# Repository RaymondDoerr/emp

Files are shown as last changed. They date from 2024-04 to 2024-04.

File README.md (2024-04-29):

# **EMP - The Excessively Magnetic Panel Mod**

Jump to: 
- [BOM and Tool List](#boms-and-tool-lists)
- [Magnet Tolerance Test](#the-magnet-tolerance-test)
- [STL Print Requirements](#stl-print-requirements)
- [Assembly](#assembly)
- [Installation](#installation)

## Description:
This mod converts every panel on the Voron to a well sealed, removable magnetic doors with all-magnetic >180° (Closer to 200°) degree hinges. All panels function as doors and are removable with no hardware what so ever, just yank 'em out!

### Quick Youtube Demo:
Demo Video (https://youtu.be/oXtChmSKKyE)

### Real Life Install Photos
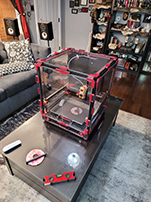
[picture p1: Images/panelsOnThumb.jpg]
Panels On
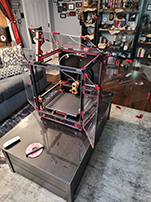
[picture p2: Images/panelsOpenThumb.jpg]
Panels Open
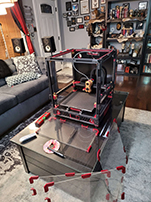
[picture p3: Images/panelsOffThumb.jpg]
Panels Off
  

### Pros:
- You can remove and reinstall all the panels in under a minute.
- Converts all 5 panels into doors with magnetic "no hardware" hinges.
- No-Glue design.
- Magnets are designed to pull into their print rather than out. So no popped out magnets!
- Provides a good chamber seal with a seal thats easy to inspect and look for gaps/flaws.
- Extremely customizable, install the mod on all the panels, only the doors, just the top, whatever you want. Mix and match!
- Pulls the panels 6mm out from the extrusions, meaning less of a chance the cable chains, hot end, wiring and other parts hitting your panels and scratching them.

### Cons:
- VHB tape. (Better than drilling holes I guess?)
- Requires a *ton* of magnets. (Approx. 188 to 236)
- While the hinges work well, they can sometimes sag a bit on the side panels just due to the overall weight. But this is just cosmetic.
- Early days of the install you may get annoyed at panel clips popping off the VHB tape. Although this is the same problem the standard Voron doors have.
- Easy install, but tedious due to so many little parts.
- The Weather seal used is a bit expensive, and not a standard Voron BOM part. (See [BOM and Tool List](#boms-and-tool-lists) for sources)
- Pulling the panels 6mm out from the extrusions has a possibility of interfering with some mods that expect the standard Voron doors and panels.

There are 2 variants of this panel mod:

### "All Doors"
This is the intended original design. Requires more magnets and hardware, but allows you to open every single panel on your Voron (including the back and top!) like a hinged door or just yank them all off with no hardware.

### "Voron Spec"
Exactly the same configuration as standard Voron panels, except with all the benefits of the magnet panels and hinges. This mod was designed with "All Doors" in mind, but for users who don't want this functionality, using the "Voron Spec" configuration will save you a ton of hardware and simplify installation while still allowing you to yank off all the panels in under 30 seconds.

# BOMs and Tool Lists:

## Tools (You have them already):
- **Small Hammer** for tapping magnets gently into place. Doesn't even have to be a hammer, you should not need much force at all. A rubber mallet also works well.
- **1x m3x20 SHCS or similar length screw** to use with the hammer. You just need an m3 SHCS long enough you can hold it with your fingers while you use the hammer.
- **Flat, solid surface** for hammering.
- **2.5mm Hex Key.**
- **Metric Ruler** at least 10cm long. (Calipers, measuring tape, etc, also work fine.)
- **Scissors** for the VHB tape. You'll want nice, sharp and clean ones.
- **A few seasons of The Office** while assembling the hardware prior to installation. (Can supplement with your show of choice.)

## "All Doors" BOM:
- **236x** - *6x3mm Disc Magnets (Grade n52 Recommended)*
  - [Source: West3d](https://west3d.com/products/6mm-x-3mm-round-neomydium-magnets)
- **89x** - *M3x8mm SHCS Screws*
- **69x** - *Hammerheads, Roll In T-Nuts or Springnuts*, <sub><sup>nice.</sup></sub>
- **20x** - *Roll In T-Nuts or Springnuts (This is in addition to above)*
- **Approx. 2 Meters / 6.7 Feet** - *0.4 Inch VHB Tape*
  - [Source: Lifetime Supply off Amazon](https://www.amazon.com/gp/product/B0CLV11RT9/)
- **Approx. 10 Meters / 33 Feet** - *9mm/8mm Weatherseal* (M-D Brand, Part No. 01025 Recommended)
  - [Source: Amazon](https://www.amazon.com/Multipurpose-Seasons-Marine-Window-Weather/dp/B000HE7YQM) - 2 Packages of 17ft.
  - [U.S. Source: Home Depot](https://www.homedepot.com/p/M-D-Building-Products-17-ft-Black-Small-Rubber-Auto-Marine-Weatherseal-for-All-Climates-01025/202066509) - 2 Packages.
  - [U.S. Source: Ace Hardware](https://www.acehardware.com/departments/building-supplies/weather-stripping-and-window-film/weather-stripping/5315445) - 2 Packages.
  - [U.S. Source: Lowes](https://www.lowes.com/pd/M-D-17-ft-x-11-32-in-Black-Rubber-Foam-Window-Weatherstrip/1038915) - 2 Packages.
  
## "Voron Spec" BOM:
- **188x** - *6x3mm Disc Magnets (Grade n52 Recommended)*
  - [Source: West3d](https://west3d.com/products/6mm-x-3mm-round-neomydium-magnets)
- **71x** - *M3x8mm SHCS Screws*
- **63x** - *Hammerheads, Roll In T-Nuts or Springnuts*
- **8x** - *Roll In T-Nuts or Springnuts (This is in addition to above)*
- **Approx. 1.8 Meters / 5.9 Feet** - *0.4 Inch VHB Tape*
  - [Source: Lifetime Supply off Amazon](https://www.amazon.com/gp/product/B0CLV11RT9/)
- **Approx. 10 Meters / 33 Feet** - *9mm/8mm Weatherseal* (M-D Brand, Part No. 01025 Recommended)
  - [Source: Amazon](https://www.amazon.com/Multipurpose-Seasons-Marine-Window-Weather/dp/B000HE7YQM) - 2 Packages of 17ft.
  - [U.S. Source: Home Depot](https://www.homedepot.com/p/M-D-Building-Products-17-ft-Black-Small-Rubber-Auto-Marine-Weatherseal-for-All-Climates-01025/202066509) - 2 Packages.
  - [U.S. Source: Ace Hardware](https://www.acehardware.com/departments/building-supplies/weather-stripping-and-window-film/weather-stripping/5315445) - 2 Packages.
  - [U.S. Source: Lowes](https://www.lowes.com/pd/M-D-17-ft-x-11-32-in-Black-Rubber-Foam-Window-Weatherstrip/1038915) - 2 Packages.
  
## Per Panel BOM (Ref. Full Part Descriptions Above):
- *Front Door* (Left and Right, **As Door**)
  - **32 Magnets, 12 Screws, 8 Hammerhead, 4 T-nuts/Springnuts**
- *Side and Top Panels* (**As Door**)
  - **44 Magnets, 17 Screws, 13 Hammerheads, 4 T-nuts/Springnuts**
- *Side and Top Panels* (**As Panel**)
  - **32 Magnets, 12 Screws, 12 Hammerheads**
- *Back Panel* (**As Door**)
  - **40 Magnets, 16 Screws, 12 Hammerheads, 4 T-nuts/Springnuts**
- *Back Panel* (**As Panel**)
  - **28 Magnets, 12 Screws, 12 Hammerheads**
  
## Per STL BOM (Ref. Full Part Descriptions Above):
- *[a]hinge_frame_SIZE.stl*
  - **4 Magnets, 3 Screws, 1 Hammerhead, 2 T-nuts/Springnuts**
- *[a]hinge_frame_bottom_SIZE.stl*
  - **4 Magnets, 2 Screws, 2 Hammerheads**
- *[a]corner_frame_SIZE.stl*
  - **2 Magnets, 2 Screws, 2 Hammerheads**
- *[a]side_frame_SIZE.stl*
  - **2 Magnets, 1 Screw, 1 Hammerhead**
- *hinge_panel_SIZE.stl*
  - **4 Magnets, 40mm VHB tape**
- *door_clip_1_SIZE.stl*
  - **2 Magnets, 20mm VHB tape**
- *door_clip_2_SIZE.stl*
  - **2 Magnets, 20mm VHB tape**
- *corner_panel_SIZE.stl*
  - **2 Magnets, 60mm VHB tape**
- *side_panel_SIZE.stl*
  - **2 Magnets, 20mm VHB tape**
  
# The Magnet Tolerance Test:
## (Don't skip!!)

Print one magnet_test.stl for every filament you plan to use for this mod, some filaments behave surprisingly differently!

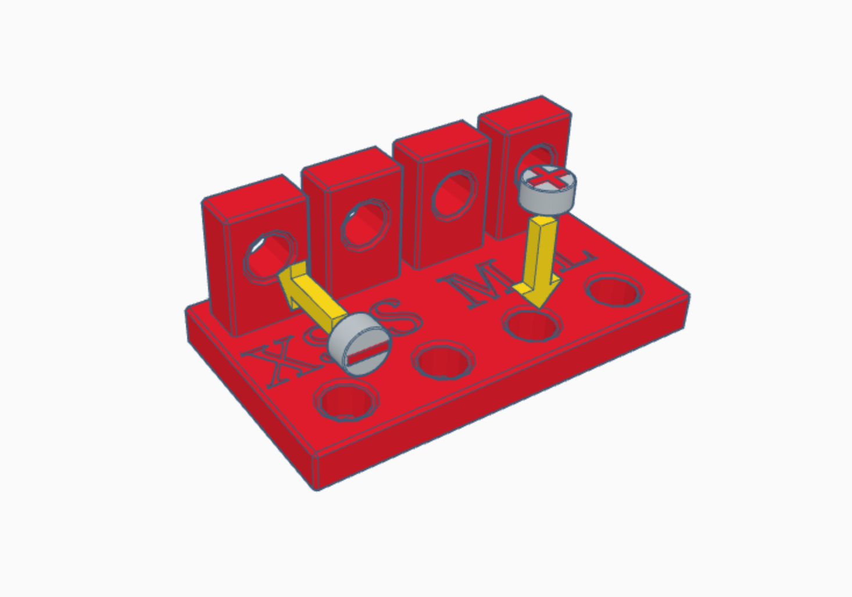
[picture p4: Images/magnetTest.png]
Magnet Test


You are looking for a "snug" but not "tight" fit. You should be able to start the magnets with your hands and some pressure. You **do not** need to seat them all the way down at this step. The fastest way to find the correct holes is to start by inserting a magnet into the *largest* bottom hole (L), if the magnet falls in or can be yanked back out with another magnet, try the next smallest hole. The goal is to find one you can shove part of the way in with your hands and can't be yanked back out with another magnet.

Repeat the same steps on the top/vertical holes. An ideal situation is you pick both the same size holes for the top and bottom. But due to print orientation and everyone's printer being just a little different, you may find yourself needing to go up or down a size on the vertical holes.

The sizes of the holes are as follows:
- XS
  - Horizontal: 6.0mm
  - Vertical: 5.9mm
- S
  - Horizontal: 6.1mm
  - Vertical: 6.0mm
- M (This is what I use)
  - Horizontal: 6.2mm
  - Vertical: 6.1mm
- L 
  - Horizontal: 6.3mm
  - Vertical: 6.2mm

# STL Print Requirements:
After selecting the hole size, now it's time to print the STLs! Select the set of parts that match the hole size you've selected. The top/vertical holes are for the hinges, the horizontal holes were for all other parts.

All prints are designed to print to Voron Spec profiles. If you have warping issues, these parts need very little cooling, all of mine were printed with only about a 5% fan speed on a Stealthburner/G2E/Revo setup. I also ran some experiments and found all the parts can be printed with no cooling what so ever, but YMMV.

All panel STLs have an optional *with_clip* variant you can print, that will add a small lip on the edge of the model making it a bit easier to catch and open the door with your fingers. If you decide to use these, you only need them on the corners you're expecting to open the door from.

## For "All Doors":
### Print with top/vertical hole size:
- **10x** *[a]hinge_frame_SIZE.stl*
- **2x** *[a]hinge_frame_bottom_SIZE.stl*
- **12x** *hinge_panel_SIZE.stl*

### Print with bottom/horizontal hole size:
- **20x** *[a]corner_frame_SIZE.stl*
- **15x** *[a]side_frame_SIZE.stl*
- **2x** *door_clip_1_SIZE.stl*
- **2x** *door_clip_2_SIZE.stl*
- **20x** *corner_panel_SIZE.stl*
- **11x** *side_panel_SIZE.stl*

## For "Voron Spec":
### Print with top/vertical hole size:
- **4x** *[a]hinge_frame_SIZE.stl*
- **4x** *hinge_panel_SIZE.stl*

### Print with bottom/horizontal hole size:
- **20x** *[a]corner_frame_SIZE.stl*
- **19x** *[a]side_frame_SIZE.stl*
- **2x** *door_clip_1_SIZE.stl*
- **2x** *door_clip_2_SIZE.stl*
- **20x** *corner_panel_SIZE.stl*
- **15x** *side_panel_SIZE.stl*

# Assembly:
## Magnets
First step is to insert all of the magnets into all of the STLs. It's very important to get the polarity correct. Be aware of the orientation of the parts in the example images.

I've found the best method to insert the magnets is to hand push in the magnet until it's halfway in, and then use the head of an M3x14mm screw and attach it to the magnet, then lightly tap the magnet down in place with a hammer. It makes assembly go much faster. Just be sure to use a flat surface so you don't blow the magnet straight through the hole!

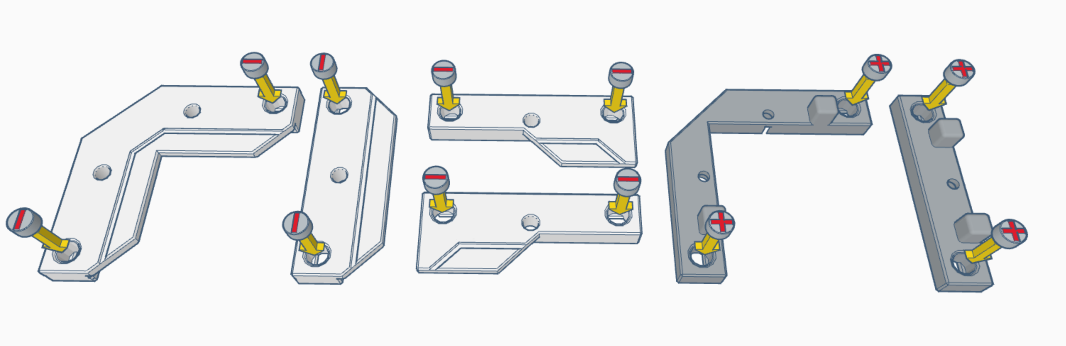
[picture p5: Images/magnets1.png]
Magnet Test

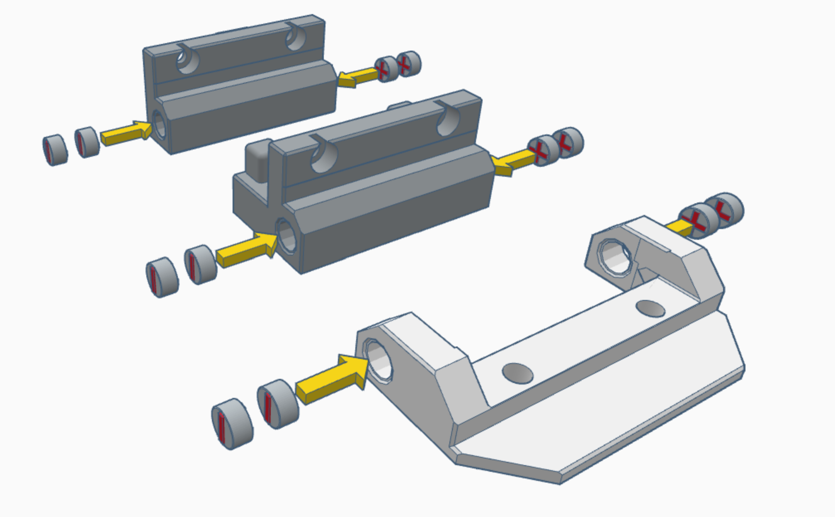
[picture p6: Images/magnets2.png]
Magnet Test


## Hardware
You may preload all the hardware **EXCEPT FOR** the T-nuts noted in red. These must be loaded into the extrusions and slid into place **after** installation of the door hinge.

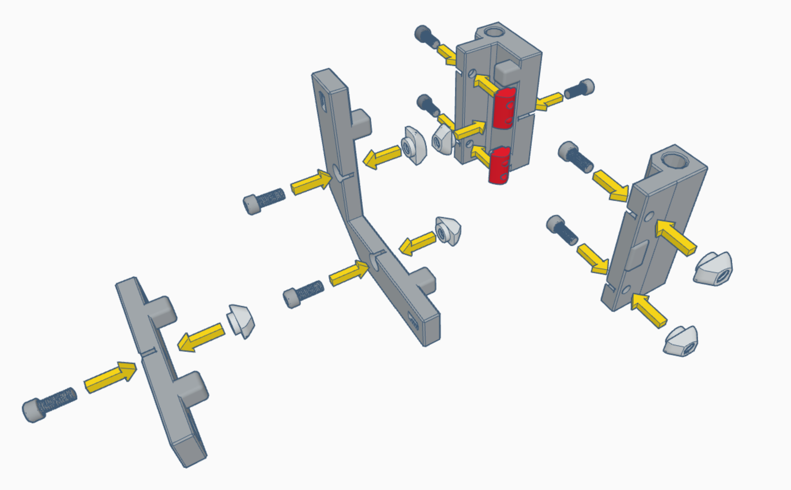
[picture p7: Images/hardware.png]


## VHB Tape
Don't skimp on the VHB tape! When installed, press down hard on the tape to get a better bond to the clips.

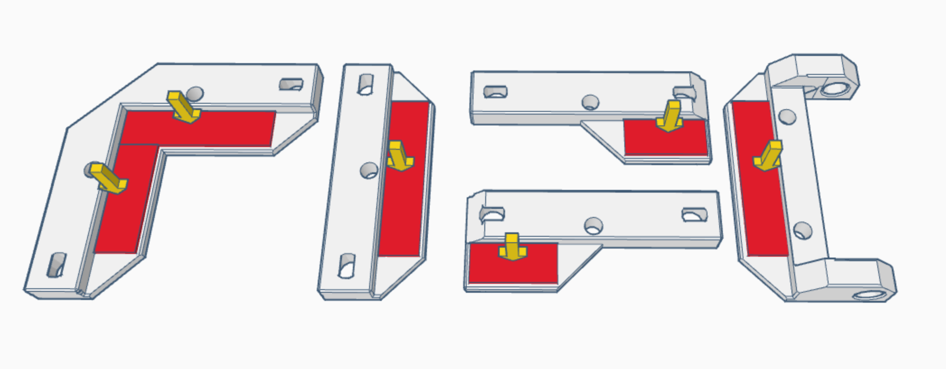
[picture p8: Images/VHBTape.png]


# Installation:

## **INSTALL GUIDE ASSUMES "ALL-DOORS" CONFIGURATION. **
### If you're doing the "Voron Spec" configuration the install guide still applies, **but** you need to supplement the 2x hinges on each panel with 1x side clips, effectively making all 4 sides of the panel symmetrical. All other steps are identical.

### Provided is a direct link to the STL Placement Reference both on Tinkercad and GitHub. Both will show you the location of every STL in 3d space. *Note its not remotely to scale, that's why everything looks ridiculously cramped.*

## View the Full Model STL Placement Reference on:
### [Fully Editable and Color Coded, Tinkercad](https://www.tinkercad.com/things/gM3WwlMIWih-emp-stl-placement-reference)
### [Uneditable and Grey Scale, GitHub](Images/placementReference.stl)

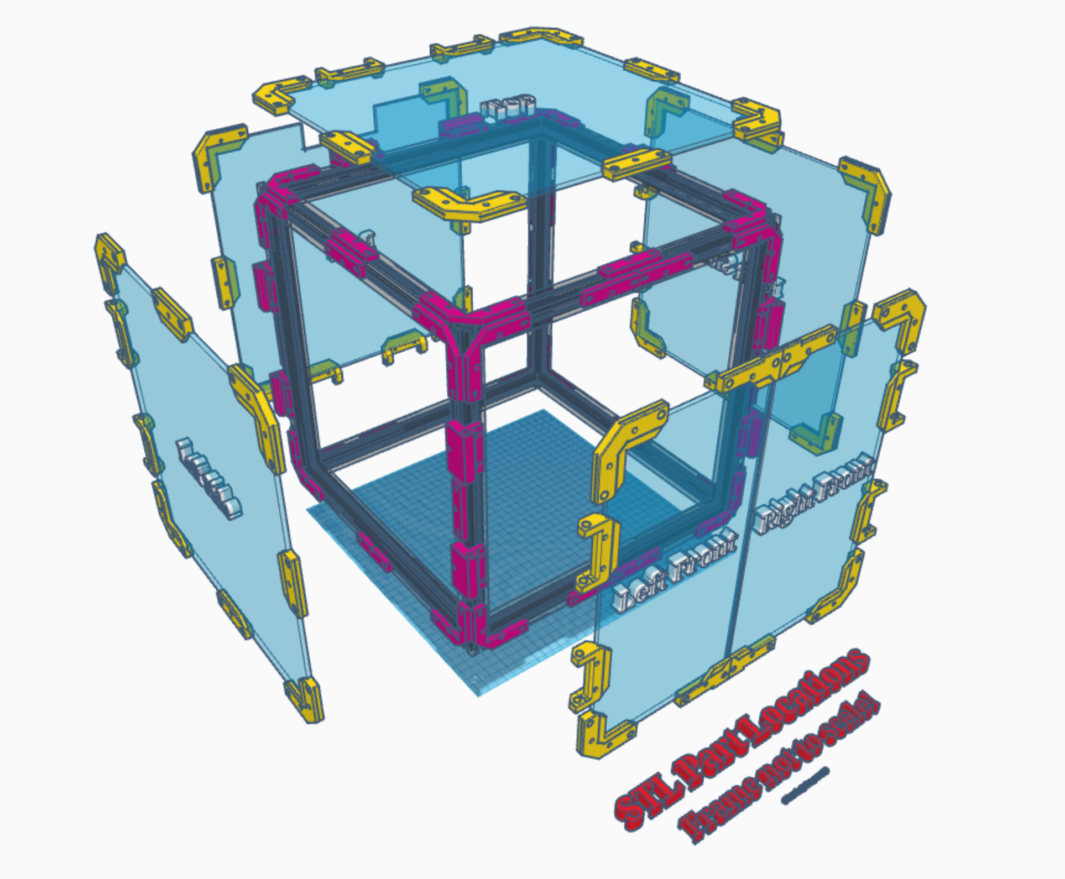
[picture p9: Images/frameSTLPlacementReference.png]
Tinkercad Reference


Refer to the following images or the Tinkercad link above for clip placement on the various panels. Apply significant pressure to the tape to ensure it sticks. In my experience, the VHB tape may be a bit weak the first few days but should all hold together just fine. I like to occasionally revisit this and push the clips down a bit more as I work through the project just to make sure they're staying down.

From here on out, all stl names will be shortened for brevity.

When installing the frame STLs, install them loose initially (just tight enough they don't fall out), you'll use the panels themselves to align the frame STLs in a future step. Place them in the same locations as the panel clips, just on the frame.

**All** Hinges are placed approximately 10cm from the edge of their respective panels.

10cm Hinge Spacing

### Left and Right Side Panels:
- *corner_panel* are placed in the 4 corners of the panel.
- *side_panel* are placed on the top, bottom and front sides of the panel, in the center.
- *hinge_panel* are placed 10cm from the edge of the panel on the back side. 
- Loosely install corner_frame, side_frame and hinge_frame STL files in the same locations as above, but on the extrusions the panel will attach to.

Side Panels Inner
Side Panels Outer

### Top Panel:
- corner_panel.stl are placed in the 4 corners of the panel.
- side_panel.stl are placed on the top, bottom and front sides in the center.
- hinge_panel.stl are placed 10cm from the edge of the panel on the back side. 
- Loosely install corner_frame, side_frame and hinge_frame STL files in the same locations as above, but on the extrusions the panel will attach to.

Top Panel Inner
Top Panel Outer

### Back Panel:
- corner_panel.stl are placed in the 4 corners.
- side_panel.stl are placed on left and right sides in the center.
- hinge_panel.stl are placed 10cm from the edge of the panel on the bottom side. 
- Loosely install corner_frame, side_frame and **hinge_frame_bottom** STL files in the same locations as above, but on the extrusions the panel will attach to.

Back Panel Inner
Back Panel Outer

### Front Doors (Left):
- corner_panel.stl are placed in the left 2 corners.
- hinge_panel.stl are placed 10cm from the edge of the panel on the left side. 
- door_clip_1.stl is placed on the bottom right corner.
- door_clip_2.stl is placed on the top right corner.
- Loosely install corner_frame, side_frame (for door_clip_1 and 2) and hinge_frame STL files in the same locations as above, but on the extrusions the doors will attach to.

### Front Doors (Right):
- corner_panel.stl are placed in the right 2 corners.
- hinge_panel.stl are placed 10cm from the edge of the panel on the right side. 
- door_clip_1.stl is placed on the top left corner.
- door_clip_2.stl is placed on the bottom left corner.
- Loosely install corner_frame, side_frame (for door_clip_1 and 2) and hinge_frame STL files in the same locations as above, but on the extrusions the doors will attach to.

Front Doors Inner
Front Doors Outer

## Attaching to extrusions

- Place one panel at a time on the extrusions and attach them to the loosened frame clips.
- Doublecheck all _frame STLs are magnetically connected to all of the _panel STLs.
- **With the panel installed and attached to the magnets**, tighten the _frame.stl parts **through** the _panel.stls with the guide holes provided. Use your hands to hold the _frame.stl and _panel.stl flush with eachother while tightening for better alignment.

Guide Holes 1
Guide Holes 2

- Anywhere there is a hinge, you may now install the Slide in T-nut or Spring nuts and slide them under the STL and tighten down the screws.

Slide In T-Nuts 1
Slide In T-Nuts 2
Slide In T-Nuts 3
Slide In T-Nuts 4

- Repeat until all panels are fulled installed.

## Installing The Weather Seal
The weather seal is placed on last so you don't accidentally tear it while installing the frame STLs, you want the weather seal placed flush along the inner side of the extrusion. If you purchased the same brand I did, many times the adhesive isn't aligned, use this to your advantage so you don't have any exposed adhesive on the frame.

You **can** place the weather seal on the panel side instead, but you may have issues with the seal pinching against some of the magnetic clips occasionally. Try to put the foam 1-2mm back from the outer edge of the panel to help prevent this.

Seal Placement 1
Seal Placement 2

Installation should be complete at this point. This is where you'll need to look at the overall fit and finish, verify everything looks nice, lined up and even when the doors/panels are installed/closed. 

Be gentle with the hinges for a few days while the VHB tape settles (ie; don't leave them hanging open on their own weight overnight). I like to give the clips a good squish against the panel here and there as I'm working with the printer, just to be sure.

### If you have serious issues with the VHB tape holding to the printed parts post install, there's a few things you can try:
- Try sanding or scratching up the surface of the clip, it will help the VHB tape grab.
- Use something heavy (books, etc) and press the panels into the clips overnight.
- If all else fails and you're working with a filament that just won't stick to the tape no matter what you do, a **very** thin layer of super glue between the tape and panel clips will perma-bond it forever. **Just be extremely careful not to get it on your panels, it'll ruin them!!!** If you must do this, I recommend applying the glue to the clip/tape and letting it fully dry before reattaching them to the panels to avoid any superglue leaking on to the panel. Ideally, no one should have to use glue for anything in this mod. But with 10,000,000 brands of ABS and ASA out there, some may just be more stubborn than others.

# Notes and Supplemental Data
### Tips
- All STL files, except the hinges, can have an additional magnet added if you want to go overkill with magnet strength or have tons of weaker magnets. Note that this will add an enormous amount of extra magnets (Roughly +70-80% more) to the BOM, and if you use n52s it'll be *ridiculously* strong.
- You can rearrange everything, adding or moving hinges and clips where you desire. 
- If you're having issues with the front doors closing (ie; hitting eachother) check to make sure clip_1 and _2 are not overlapping the edge of the panel. Also sometimes just fiddling with the hinges can improve fit and finish.
- If you're using hammerheads for the first time, make sure they actually are holding your part in. They can easily miss the extrusions and just tighten into the plastic.
- The corner_panel/frame STLs on the front doors are technically optional. They're more for ascetics than functionality.
- You can remove 1 magnet from each door_clip_1 and door_clip_2 if you find the front door too strong to open. (Or just use weaker magnets if you have them.)
- You can also remove almost all the side_panel/frame STLs from the entire build, although you may want to double-up on magnets in the corner_panel STLs if it makes the panel too weak. 

### Mod Compatibility
- [The raw STL files on Tinkercad.](https://www.tinkercad.com/things/bFb7dxLxUFV-excessively-magnetic-panel-mod-parts)
- This has not been tested with the [Clicky-Clack Fridge Door Mod](https://github.com/tanaes/whopping_Voron_mods/tree/main/clickyclacky_door), but should theoretically work if you omit the side clips interfering with the Fridge Mod's hinge. There is a possibility it may rub against the side panel. Please let me know if this is an issue!
- This should work with just about any mod that doesn't have an issue with the panels being pushed outwards about 6-8mm from the frame.

### Coming Soon (Before full release)
- A magnetic door handle of some sort.
- Small magnetic arms to prop doors open.

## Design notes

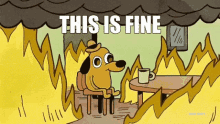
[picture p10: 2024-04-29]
Images/this-is.gif

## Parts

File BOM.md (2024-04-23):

# BOMs and Tool Lists:

## Tools (You have them already):
- **Small Hammer** for tapping magnets gently into place. Doesn't even have to be a hammer, you should not need much force at all. A rubber mallet also works well.
- **1x m3x20 SHCS or similar length screw** to use with the hammer. You just need an m3 SHCS long enough you can hold it with your fingers while you use the hammer.
- **Flat, solid surface** for hammering.
- **2.5mm Hex Key.**
- **Metric Ruler** at least 10cm long. (Calipers, measuring tape, etc, also work fine.)
- **Scissors** for the VHB tape. You'll want nice, sharp and clean ones.
- **A few seasons of The Office** while assembling the hardware prior to installation. (Can supplement with your show of choice.)

## "All Doors" BOM:
- **236x** - *6x3mm Disc Magnets (Grade n52 Recommended)*
  - [Source: West3d](https://west3d.com/products/6mm-x-3mm-round-neomydium-magnets)
- **89x** - *M3x8mm SHCS Screws*
- **69x** - *Hammerheads, Roll In T-Nuts or Springnuts*, <sub><sup>nice.</sup></sub>
- **20x** - *Roll In T-Nuts or Springnuts (This is in addition to above)*
- **Approx. 2 Meters / 6.7 Feet** - *0.4 Inch VHB Tape*
  - [Source: Lifetime Supply off Amazon](https://www.amazon.com/gp/product/B0CLV11RT9/)
- **Approx. 10 Meters / 33 Feet** - *9mm/8mm Weatherseal* (M-D Brand, Part No. 01025 Recommended)
  - [Source: Amazon](https://www.amazon.com/Multipurpose-Seasons-Marine-Window-Weather/dp/B000HE7YQM) - 2 Packages of 17ft.
  - [U.S. Source: Home Depot](https://www.homedepot.com/p/M-D-Building-Products-17-ft-Black-Small-Rubber-Auto-Marine-Weatherseal-for-All-Climates-01025/202066509) - 2 Packages.
  - [U.S. Source: Ace Hardware](https://www.acehardware.com/departments/building-supplies/weather-stripping-and-window-film/weather-stripping/5315445) - 2 Packages.
  - [U.S. Source: Lowes](https://www.lowes.com/pd/M-D-17-ft-x-11-32-in-Black-Rubber-Foam-Window-Weatherstrip/1038915) - 2 Packages.
  
## "Voron Spec" BOM:
- **188x** - *6x3mm Disc Magnets (Grade n52 Recommended)*
  - [Source: West3d](https://west3d.com/products/6mm-x-3mm-round-neomydium-magnets)
- **71x** - *M3x8mm SHCS Screws*
- **63x** - *Hammerheads, Roll In T-Nuts or Springnuts*
- **8x** - *Roll In T-Nuts or Springnuts (This is in addition to above)*
- **Approx. 1.8 Meters / 5.9 Feet** - *0.4 Inch VHB Tape*
  - [Source: Lifetime Supply off Amazon](https://www.amazon.com/gp/product/B0CLV11RT9/)
- **Approx. 10 Meters / 33 Feet** - *9mm/8mm Weatherseal* (M-D Brand, Part No. 01025 Recommended)
  - [Source: Amazon](https://www.amazon.com/Multipurpose-Seasons-Marine-Window-Weather/dp/B000HE7YQM) - 2 Packages of 17ft.
  - [U.S. Source: Home Depot](https://www.homedepot.com/p/M-D-Building-Products-17-ft-Black-Small-Rubber-Auto-Marine-Weatherseal-for-All-Climates-01025/202066509) - 2 Packages.
  - [U.S. Source: Ace Hardware](https://www.acehardware.com/departments/building-supplies/weather-stripping-and-window-film/weather-stripping/5315445) - 2 Packages.
  - [U.S. Source: Lowes](https://www.lowes.com/pd/M-D-17-ft-x-11-32-in-Black-Rubber-Foam-Window-Weatherstrip/1038915) - 2 Packages.

## Per STL BOM (Ref. Full Part Descriptions Above):
- *[a]hinge_frame_<SIZE>.stl*
  - **4 Magnets, 3 Screws, 1 Hammerhead, 2 T-nuts/Springnuts**
- *[a]hinge_frame_bottom_<SIZE>.stl*
  - **4 Magnets, 2 Screws, 2 Hammerheads**
- *[a]corner_frame_<SIZE>.stl*
  - **2 Magnets, 2 Screws, 2 Hammerheads**
- *[a]side_frame_<SIZE>.stl*
  - **2 Magnets, 1 Screw, 1 Hammerhead**
- *hinge_panel_<SIZE>.stl*
  - **4 Magnets, 40mm VHB tape**
- *door_clip_1_<SIZE>.stl*
  - **2 Magnets, 20mm VHB tape**
- *door_clip_2_<SIZE>.stl*
  - **2 Magnets, 20mm VHB tape**
- *corner_panel_<SIZE>.stl*
  - **2 Magnets, 60mm VHB tape**
- *side_panel_<SIZE>.stl*
  - **2 Magnets, 20mm VHB tape**
  
# Ignore below this line, I'm just too lazy to put notes anywhere else at the moment..

### Per STL breakdown for All Doors:
- [a]hinge_frame_<SIZE>.stl
  - 48 Magnets, 36 Screws, 12 Hammerhead, 24 T-nuts
- [a]corner_clip_frame_<SIZE>.stl
  - 40 Magnets, 40 Screws, 40 Hammerheads
- [a]side_clip_frame_<SIZE>.stl
  - 30 Magnets, 15 Screw, 15 Hammerhead
- hinge_panel_<SIZE>.stl
  - 48 Magnets, 480mm VHB tape
- door_clip_1_<SIZE>.stl
  - 4 Magnets, 40mm VHB tape
- door_clip_2_<SIZE>.stl
  - 4 Magnets, 40mm VHB tape
- corner_clip_panel_<SIZE>.stl
  - 40 Magnets, 1200mm VHB tape
- side_clip_panel_<SIZE>.stl
  - 22 Magnets, 220mm VHB tape
  
### Per STL breakdown for Voron Spec:
- [a]hinge_frame_<SIZE>.stl
  - 16 Magnets, 12 Screws, 4 Hammerhead, 8 T-nuts
- [a]corner_clip_frame_<SIZE>.stl
  - 40 Magnets, 40 Screws, 40 Hammerheads
- [a]side_clip_frame_<SIZE>.stl
  - 38 Magnets, 19 Screw, 19 Hammerhead 
- hinge_panel_<SIZE>.stl
  - 16 Magnets, 160mm VHB tape
- door_clip_1_<SIZE>.stl
  - 4 Magnets, 40mm VHB tape
- door_clip_2_<SIZE>.stl
  - 4 Magnets, 40mm VHB tape
- corner_clip_panel_<SIZE>.stl
  - 40 Magnets, 1200mm VHB tape
- side_clip_panel_<SIZE>.stl
  - 30 Magnets, 300mm VHB tape

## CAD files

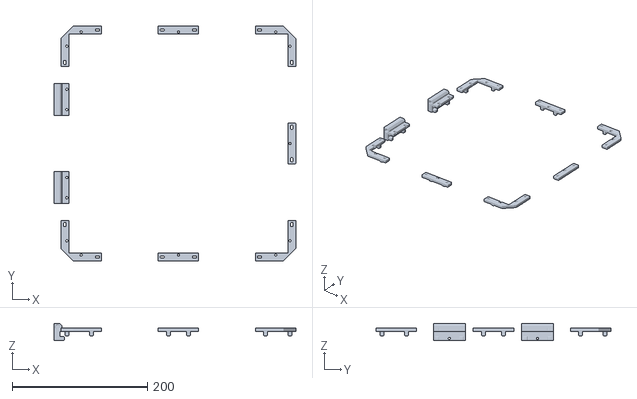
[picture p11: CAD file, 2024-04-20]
Images/placement_reference.stl
358.2 x 348.0 x 25.2

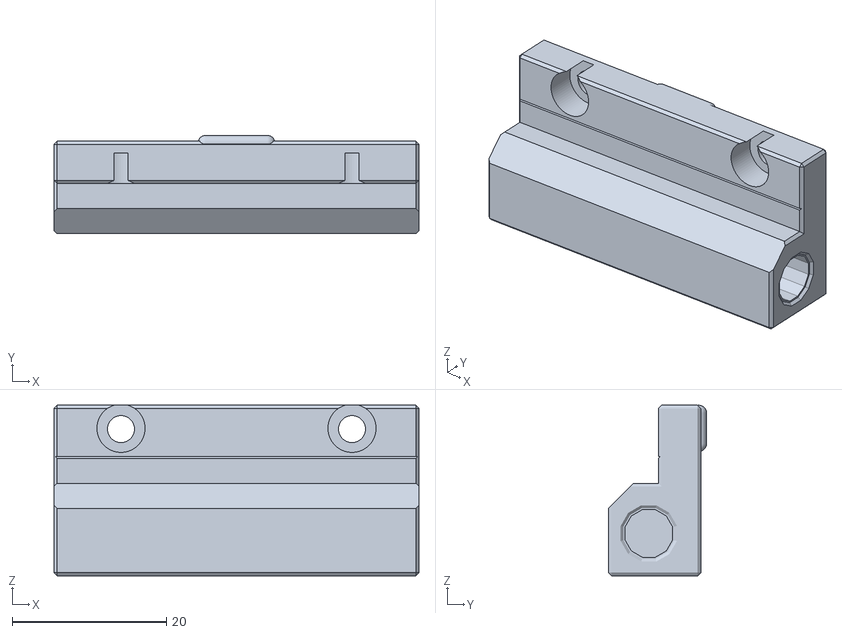
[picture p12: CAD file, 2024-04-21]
STL/alphaSTLs/[a]hinge_frame_bottom_l.stl
47.4 x 12.8 x 22.1

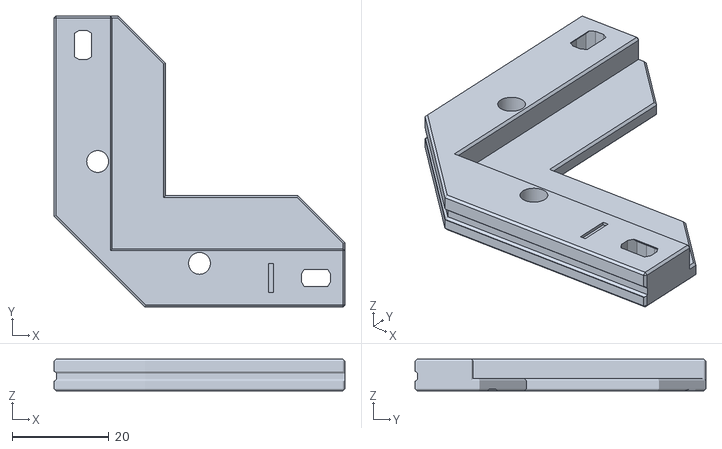
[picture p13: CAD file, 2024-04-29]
STL/extra_small/corner_panel_extra_small.stl
60.0 x 60.0 x 6.50

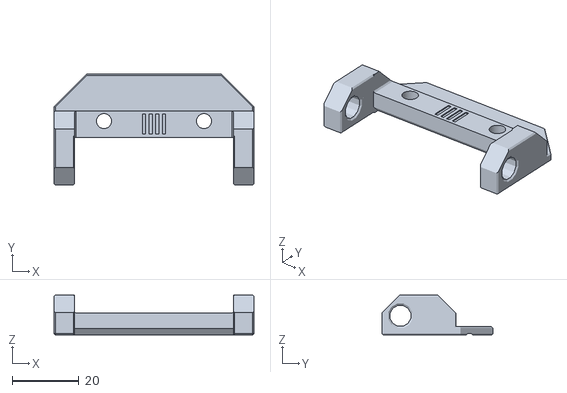
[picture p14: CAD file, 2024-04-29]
STL/large/hinge_panel_large.stl
60.0 x 33.2 x 12.0

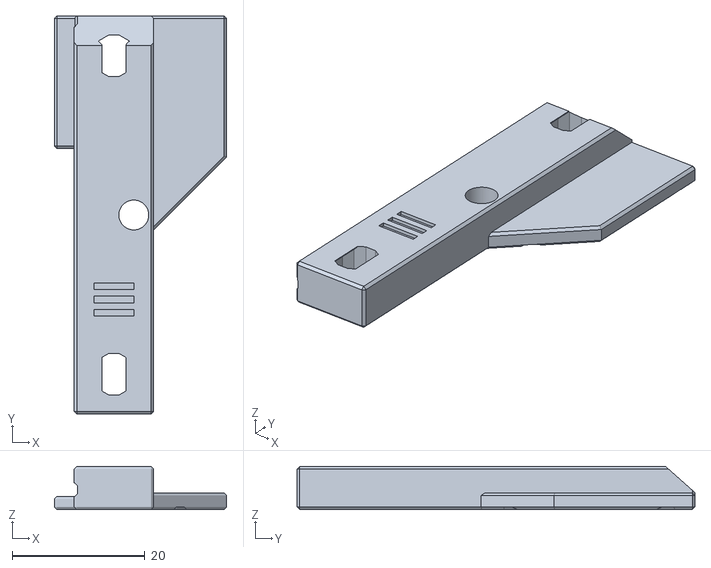
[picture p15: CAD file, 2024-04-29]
STL/medium/door_clip_2_medium.stl
26.0 x 60.0 x 6.50

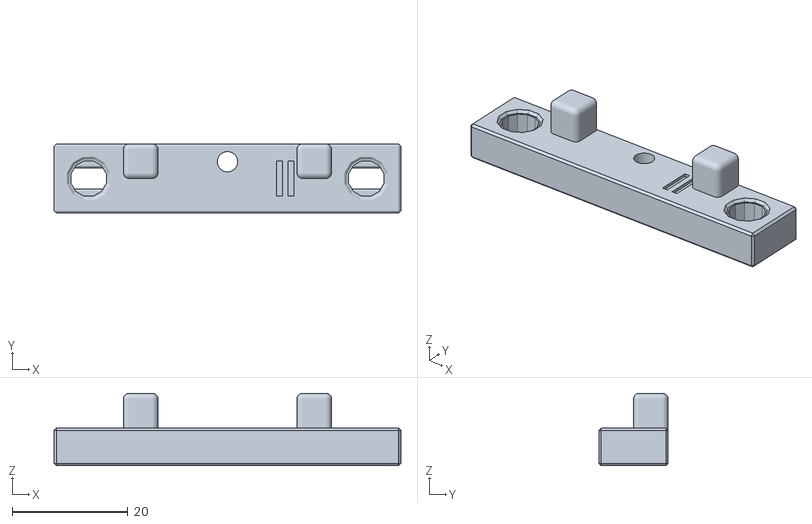
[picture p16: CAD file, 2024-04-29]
STL/small/[a]side_frame_small.stl
60.0 x 12.0 x 12.5

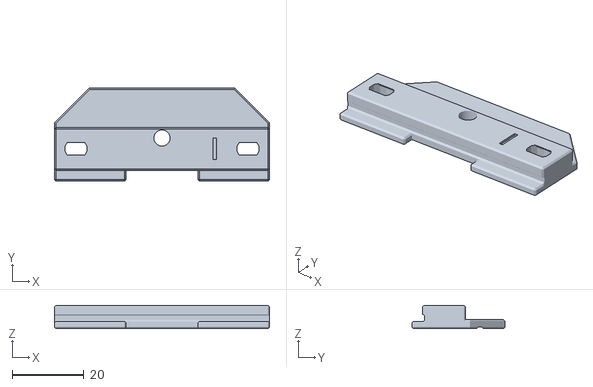
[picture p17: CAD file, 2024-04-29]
STL/extra_small/side_panel_with_clip_extra_small.stl
60.0 x 26.0 x 6.50

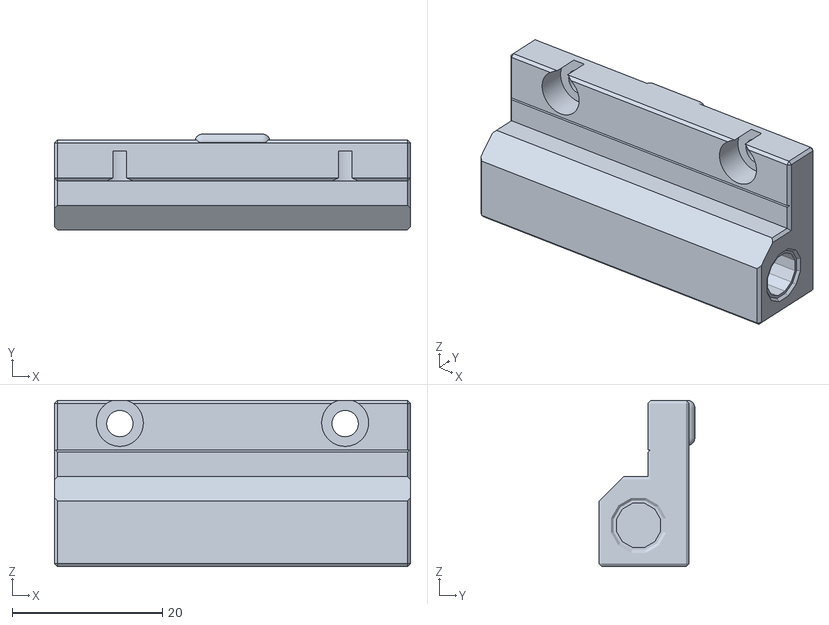
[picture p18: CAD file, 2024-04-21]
STL/alphaSTLs/[a]hinge_frame_bottom_xs.stl
47.4 x 12.8 x 22.1

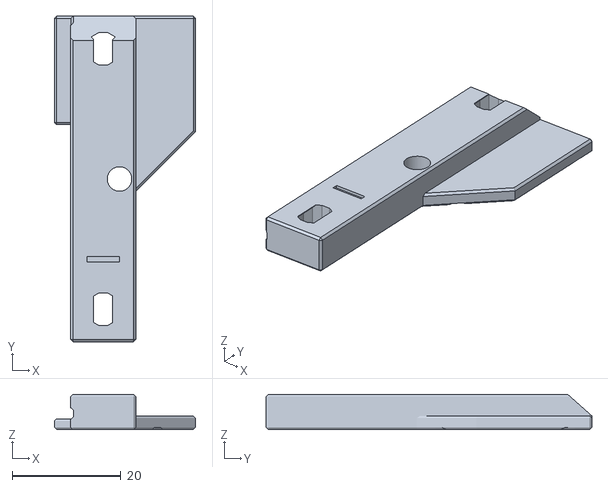
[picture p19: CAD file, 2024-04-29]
STL/extra_small/door_clip_2_extra_small.stl
26.0 x 60.0 x 6.50

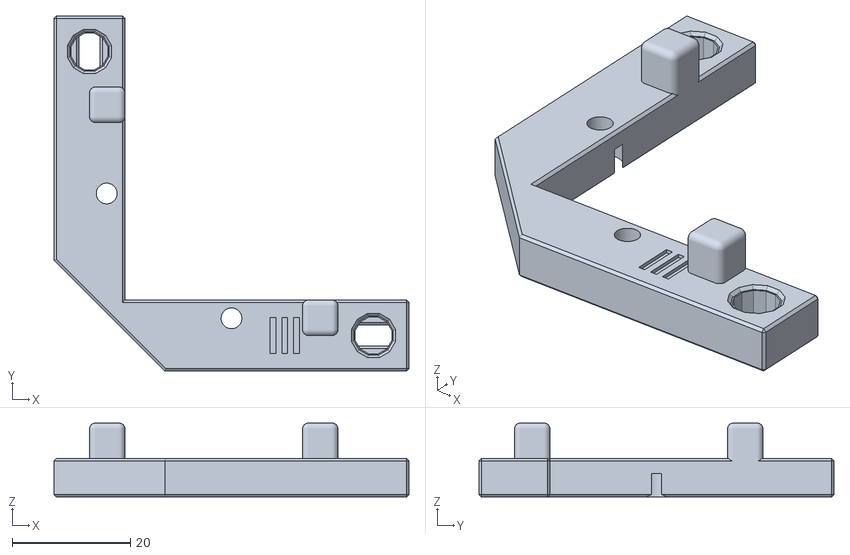
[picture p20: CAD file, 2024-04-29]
STL/medium/[a]corner_frame_medium.stl
60.0 x 60.0 x 12.5

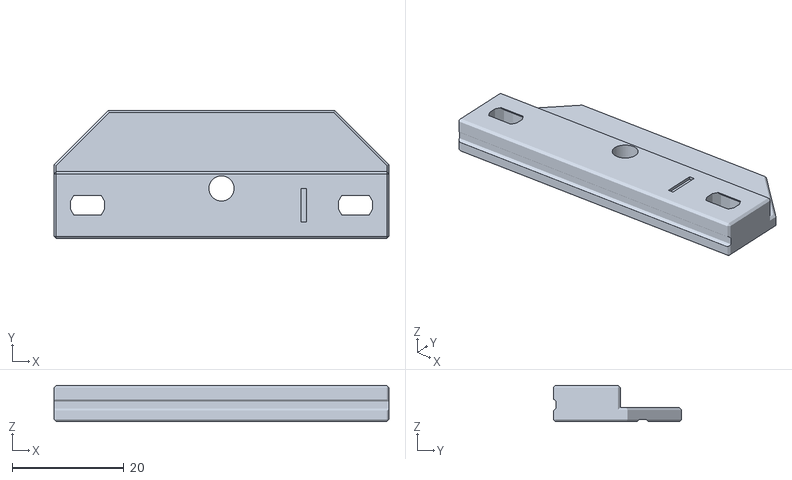
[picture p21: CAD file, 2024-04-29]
STL/extra_small/side_panel_extra_small.stl
60.0 x 23.0 x 6.50

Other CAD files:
STL/alphaSTLs/[a]hinge_frame_bottom_m.stl
STL/large/door_clip_2_large.stl
STL/medium/[a]side_frame_medium.stl
STL/small/hinge_panel_small.stl
STL/large/[a]side_frame_large.stl
STL/small/door_clip_1_small.stl
STL/alphaSTLs/[a]hinge_frame_bottom_s.stl
STL/alphaSTLs/[a]corner_frame_l.stl
STL/alphaSTLs/[a]corner_frame_m.stl
STL/alphaSTLs/[a]corner_frame_s.stl
STL/alphaSTLs/[a]corner_frame_xs.stl
STL/alphaSTLs/[a]hinge_frame_l.stl
STL/alphaSTLs/[a]hinge_frame_m.stl
STL/alphaSTLs/[a]hinge_frame_s.stl
STL/alphaSTLs/[a]hinge_frame_xs.stl
STL/alphaSTLs/[a]side_frame_l.stl
STL/alphaSTLs/[a]side_frame_m.stl
STL/alphaSTLs/[a]side_frame_s.stl
STL/alphaSTLs/[a]side_frame_xs.stl
STL/alphaSTLs/corner_panel_l.stl
STL/alphaSTLs/corner_panel_m.stl
STL/alphaSTLs/corner_panel_s.stl
STL/alphaSTLs/corner_panel_xs.stl
STL/alphaSTLs/door_clip_1_l.stl
STL/alphaSTLs/door_clip_1_m.stl
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

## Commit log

2024-04-19 First Upload.
    yolo
    [[a]corner_frame_l.stl, [a]corner_frame_m.stl, [a]corner_frame_s.stl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]
2024-04-19 whats this button do
2024-04-19 Fixed STLs
    [[a]corner_frame_l.stl, [a]corner_frame_m.stl, [a]corner_frame_s.stl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]
2024-04-21 More Docs
    [[a]hinge_frame_bottom_l.stl, [a]hinge_frame_bottom_m.stl, [a]hinge_frame_bottom_s.stl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]
2024-04-21 Fixed reference STL
2024-04-29 New STLs!
    [[a]corner_frame_extra_small.stl, [a]corner_frame_l.stl, [a]corner_frame_large.stl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]
